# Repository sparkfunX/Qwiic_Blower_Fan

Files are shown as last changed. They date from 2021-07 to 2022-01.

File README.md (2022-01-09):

Qwiic Blower Fan
========================================

[Qwiic Blower Fan

[*Qwiic Blower Fan (SPX-18561)*](https://www.sparkfun.com/products/18561)

The unmistakable sounds of a tiny cooling fan spooling up usually means you've sat your laptop on a soft surface, or launched one too many tabs in your browser. It's a textbook cry for help from all of our favorite consumer electronics but what if your next hardware project could also complain about overheating? Well now it can!

In all seriousness, though, sometimes you need to move a little air around. Whether for active cooling or ventilation, a tiny fan can make a big difference. However, a tiny fan also has tiny wires which can make it difficult to work with. We've remedied this issue by mounting it to a board along with the mating flat-flex connector, a voltage booster and an ATtiny-based driver so you can power and control the fan over the Qwiic bus.

The control firmware monitors the tachometer output of the fan in order to implement PI Control over the fan speed, allowing you to set your desired speed in real units. It's also possible to disable the PI control loop and set the speed as a proportion of the maximum. The accompanying Arduino library includes example code for controlling the fan, tweaking settings, and even setting the fan speed based on an attached Qwiic Temperature Sensor and a lookup table.

We're unable to find a datasheet for this fan in particular (which is intended to replace the OEM fan in a Nintendo Switch)

Heads Up! This device draws enough power that it operates at the upper limit of the Qwiic bus. If there are few other devices on the bus and the fan is not allowed to rapidly change throttle, it is possible to power this fan directly from the bus. In some applications, however, it may be necessary to provide the blower fan with a dedicated 3.3V supply.

Repository Contents
-------------------

* **/Firmware** - Control firmware for the ATtiny
* **/Hardware** - Eagle design files (.brd, .sch)
* **/Production** - Panelized hardware files for production

License Information
-------------------

This product is _**open source**_! 

Please review the LICENSE.md file for license information. 

If you have any questions or concerns on licensing, please contact technical support on our [SparkFun forums](https://forum.sparkfun.com/viewforum.php?f=152).

Distributed as-is; no warranty is given.

- Your friends at SparkFun.

_<COLLABORATION CREDIT>_

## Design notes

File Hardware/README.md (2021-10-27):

# Qwiic_Blower_Fan
2-Wire Controllable Nintendo Switch Cooling Fan Breakout

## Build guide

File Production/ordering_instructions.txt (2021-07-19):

panel size, 147x152mm
PCB thickness, 1.6mm
number of layers, 2
soldermask color, Black
silkscreen color, White
oz copper, 1oz
finish, HASL lead free
stencils, top
pcs per panel, 6
min trace width, 0.1524mm / 0.0060in
min drill size, 0.3000mm / 0.0118in

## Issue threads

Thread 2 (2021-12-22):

Qwiic Fan Controller Firmware Bugs

dlkeng, 2021-12-22:
In reviewing and testing the "**Qwiic_Fan_Controller.ino**" firmware, I have observed and run into the following bugs:

1. In function `updateSettings()`: line **266**: What if `registerMap[WIRE_ADDR]` is an invalid I2C address? The `receiveEvent()` allows any value to be written to any register!
2. In function `requestEvent()`: line **388**: `requestEvent()` always writes 17 bytes. What if `registerIndex` is greater than zero? It will then return bytes beyond the end of `registerMap[]`! (not fatal, but not good!)
3. In function `receiveEvent()`: line **435**:
   -  What if `receivedCommands[0]` is an invalid register address? It will then allow bytes to be written beyond the end of `registerMap[]`!
   - What if `bytesReceived` is greater than `MAX_SENT_BYTES`? It will then allow whatever is in the memory beyond the end of `receivedCommands[]` to be written to `registerMap[]`!
   - What prevents writing beyond the end of `registerMap[]`? For example, assume `receivedCommands[0]` is `TRIMMER_DISABLE` and multiple bytes were sent. Any received bytes after the first one would be written to memory beyond the end of `registerMap[]`!

In summary, the `receiveEvent()` callback function has some serious memory integrity issues!

NPoole, 2021-12-30:
Thanks for the code review. Yeah this all looks about right.

1. I removed address validation during debugging and forgot to put it back
2. This is designed to wrap around so that you can read sequentially from every register but I forgot to implement the actual looping part. The fact that it always writes the entire register map is a consequence of the way the wire library ISRs work. It should be OK once it loops instead of wandering off into unknown memory.
3.  Same problem as 2 in reverse. I'll implement cyclic writes and register validation.

I'll correct these issues and make the new firmware available as soon as I can.

NPoole, 2022-01-09:
v11 addresses all of these issues to my satisfaction. Please feel free to check it out,

- Any address may be written to registerMap[WIRE_ADDR] but the address is validated before applying the change and committing it to EEPROM. If the address is outside of the valid range (0x08 to 0x77 inclusive)
- requestEvent() now writes all register values starting from the requested register to the end of the map and stops
- receiveEvent() can no longer write past the end of the register map, it will wrap around when it reaches the end

Please also keep in mind that the **current firmware now compiles to 8094 bytes and the target uC only has 8192 bytes of progmem**. While some features/fixes may not be robust, trade-offs have to be made. I believe (with the addition of i2c address validation) that any wayward register writes could now, in the worst case, be corrected by power cycling the device, which may not be a high bar to clear, but thanks to your testing we now clear it.

Closed 2022-01-09.

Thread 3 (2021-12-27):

QWIIC BLOWER FAN EXAMPLE FAILS TO RUN

JimKruk, 2021-12-27:
https://www.sparkfun.com/products/18561 Qwiic Blower Fan

downloaded the code from here: https://github.com/sparkfun/SparkFun_Qwiic_Fan_Arduino_Library

Example1_SetFanSpeed using a blackboard. when I plug in the USB the fan comes on before any code is downloaded. After compiling and downloading it see this error in setup:

Qwiic Blower Fan Example 1: Setting the Fan Speed
Device failed to setup - stopping
thoughts ?

dlkeng, 2021-12-29:
That is usually caused by the incorrect I2C address being used. By default, the **Qwiic Fan Arduino Library** uses the default I2C address of **0x36**. Your Sparkfun Qwicc Blower Fan has probably had its I2C address changed. You probably need to run an I2C scan sketch to determine what the I2C address your Sparkfun Qwicc Blower Fan is using.

Once you determine its I2C address, you can change the "_blower.begin()_" line in the Example1_SetFanSpeed to "_blower.begin(Wire,_ <your_I2C_address>_)_" and it should then work.

JimKruk, 2021-12-29:
Hi Dan
Here is the code I am using based on example1 I added a I2C scan function
but it says no devices found, When I try and pass a value of 36 I get a
compiler error,  I am using a blackboard and arduino 1.8.10

no matching function for call to 'PCFan::begin(int)'
thanks

/*
  This is a example written for the SparkFun Qwiic Blower Fan
  SparkFun sells these at its website: www.sparkfun.com
  Do you like this library? Help support SparkFun. Buy a board!
  https://www.sparkfun.com/products/18561

  Written by Nick Poole @ SparkFun Electronics, October 258h, 2021

  This example code demonstrates how to set and get the fan speed
  by randomly generating fan speeds between 0 and 8000 RPM
  and sending them to the board. It then reads the fan tachometer for
  comparison.

  https://github.com/sparkfun/SparkFun_Qwiic_Fan_Arduino_Library

  Development environment specifics:
  Arduino IDE 1.8.7

  This program is distributed in the hope that it will be useful,
  but WITHOUT ANY WARRANTY; without even the implied warranty of
  MERCHANTABILITY or FITNESS FOR A PARTICULAR PURPOSE. See the
  GNU General Public License for more details.

  You should have received a copy of the GNU General Public License
  along with this program.  If not, see <http://www.gnu.org/licenses/>.
*/

#include <SparkFun_Qwiic_Fan_Arduino_Library.h>
#include <Wire.h>
// Initialize the board
PCFan Blower;

void setup()
{
  Wire.begin();
  Serial.begin(115200);    // Start serial communication at 115200 baud
  scanI2C();
  Serial.println("Qwiic Blower Fan Example 1: Setting the Fan Speed");
  if (Blower.begin(36) == true) // Function to check if the board will ACK
  {
    Serial.println("Begin");
  }
  else
  {
    Serial.println("Device failed to setup - stopping");
    while (1); // Just sit and do nothing
  }
  Blower.disableFan();
}

void loop() {

  // Pick a random speed between 0 and 8000 RPM (In 1000 RPM increments)
  int randSpeed = random(0,8) * 1000;

  // Print the number to the terminal
  Serial.print("Setting Fan Speed to ");
  Serial.print(randSpeed);
  Serial.println(" RPM");

  // Set the fan speed
  Blower.setFanSpeed(randSpeed);

  // For the next 3 seconds, once per second, ask the board for a
tachometer reading
  // and report it to the terminal
  for(byte i = 0; i < 3; i++){
    delay(1000);
    Serial.print("Tachometer Reads ");
    Serial.print(Blower.getFanSpeed());
    Serial.println(" RPM");
  }

  // Print an empty line to make the terminal more readable
  Serial.println();
  delay(1000);

}

void scanI2C()
{
  byte error, address;
  int nDevices;

  Serial.println("Scanning I2C devices...");

 nDevices = 0;
 for (address = 1; address < 127; address++ )
  {
    // The i2c_scanner uses the return value of
    // the Write.endTransmisstion to see if
    // a device did acknowledge to the address.
    Wire.beginTransmission(address);
    error = Wire.endTransmission();

    if (error == 0)
    {
      Serial.print(F("I2C device found at address 0x"));
      Serial.println(address, HEX);
      nDevices++;

    }
    else if (error == 4)
    {
      Serial.print("Unknown error at address 0x");
      if (address < 16)
        Serial.print("0");
      Serial.println(address, HEX);
    }
  }

  // clear row 3 that was display i2c devices found

  if (nDevices == 0)
  {
    Serial.println("No I2C devices found\n");

  }
  else
  {
    Serial.print(nDevices);Serial.println(" I2C devices found");

  }
  delay(1000);           // wait 5 seconds for next scan

}

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

JimKruk, 2021-12-29:
fyi I added a second I2C device (TMP117) and it discovered that but not the
fan so the scan routine seems ok

Scanning I2C devices...
I2C device found at address 0x48
1 I2C devices found

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

PaulZC, 2021-12-29:
Hi @JimKruk ,

Which processor board are you using? If you're using an Artemis-based board, this might be a clock-stretching issue.

Have you tried ignoring the result of ```Blower.begin()```? What happens if you comment the ```while(1);  // Just sit and do nothing```? Does the rest of the code run normally?

Best wishes,
Paul

dlkeng, 2021-12-29:
Jim,
The fact you can scan and find another I2C device says you might have a problem with your Qwiic Blower Fan. Are you sure you are providing about 3.3V to it? You can measure it on the labeled point near the edge on the top or bottom of the board. Also, make sure your SDA and SCL (and GND) connections are all OK in the Qwiic wiring cable if that's what you're using.

If your Qwiic Blower Fan is getting power and your connections are OK, then you might have a defective Qwiic Blower Fan. If that's the case, I'm afraid I can't help you. (If you are familiar with electronics troubleshooting, you could also check that pin 2 of the 6-pin AVR ISP Connector holes on the back side of the board measures about 5V. If not, there could be a problem with the onboard U3 DC-DC Converter - see schematic. Everything on the Qwiic Blower Fan runs on 5V)

Also, two things about the use of the alternate "_button.begin()_". First, you are missing the "**Wire**" parameter and second, the address you used was decimal and you probably want the hex number with a leading '0x' (that's what the scan tool provides). That's why you had the compile error. The "_begin()_" optionally takes two parameters: **TwoWire &wirePort** and **uint8_t deviceAddress**.

JimKruk, 2021-12-29:
Hi Paul
I am using the sparkfun blackboard with a qwiic connection I am not home
right now but will try commenting out the loop and let you know. Kinda
doubt it will work since the i2c scanner does not see anything.
Thanks
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

JimKruk, 2021-12-29:
Hi Dan
Do you have an example of what I would code on the begin() line ? When I
get home home I will try and get some voltage measurements. I am using a
blackboard and a qwiic cable so no wiring per say.
Thanks

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

dlkeng, 2021-12-29:
Jim,
Assuming you can get the I2C scan to find your Fan, for example:
    `I2C device found at address 0x40`

then use:
  `if (Blower.begin(Wire, 0x40) == true)`

in place of the default: `if (Blower.begin() == true)`
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
JimKruk, 2022-01-05:
Awesome, thanks for the update Nick.  Btw Russell Turner from sf emailed me
about this also, not sure he is coordinating with you on this.

Curious, is this a firmware issue or just bad luck on the two fans I
received?
Thanks

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

NPoole, 2022-01-05:
I just messaged him to make sure we're not duplicating our efforts

It seems to me that there was no firmware on the unit that you received and right now we're trying to determine whether a few units were faulty or if an entire batch made it into stock without getting programmed.

JimKruk, 2022-01-05:
Ok, thanks.

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

JimKruk, 2022-01-06:
Hi Nick
I received replacement fans today, order # 6900103, still not working, the i2c scan routine does not detect it.  If it is a firmware update and something that is documented or someone has time to walk me through I am willing to try it vs mailing back and forth, let me know, thanks

JimKruk, 2022-01-07:
Hi Nick
Russell just replied and said you would take the lead on this. If you want me to attempt updating firmware and can walk me through it I’ll try.  I have no special hardware, etc but willing to try

JimKruk, 2022-01-10:
Hi Nick
Was wondering if you were able to get an updated firmware to work ?  I have four boards now if you want me to try and test something, thanks

NPoole, 2022-01-12:
Hi Jim!
Sorry for the delay. The problem you have isn't that you got a firmware that doesn't work, but that you didn't get any firmware at all. As far as I can tell, we've somehow sent you a number of completely unprogrammed units.

You could program the firmware on these units using a SparkFun Redboard/Arduino Uno/etc. as a programmer, if you want to attempt it, I'll give you instructions here. I've just tried it on my end to make sure it works.

**Step 1) Program Redboard with the ArduinoISP sketch**
Since you mentioned that you don't have a programmer on-hand, we're gonna use a Redboard (or other Uno-style Arduino board) as a programmer. The Arduino IDE actually includes the sketch for doing this as a Built-In Example.

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

Open this sketch and Upload it

**Step 2) Attach the RedBoard to your Qwiic Fan Blower**
Now you'll need to connect the RedBoard to the programming header on the Qwiic Blower Fan. The programming header is the 2x3 pin header on the backside of the board. I soldered pins to mine during firmware development, and this is the most reliable way, but you could theoretically just push header pins against it to make a temporary connection.

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

Here is the pinout of the Qwiic Blower programming header. Pin 1 is the one marked with a line on the silkscreen:
```
Pin 1*: MISO  | Pin 2: 3.3V
Pin 3: SCK    | Pin 4: MOSI
Pin 5: D10    | Pin 6: GND
```

**Step 3) Install the board package**
Before you can program the Qwiic Blower, you'll need the Arduino Board Package for the attiny841 that the board is based on. You can do this through the Arduino Board Manager. Search "attinycore" and install the package as shown

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

**Step 4) Open the firmware in Arduino**
You can find the firmware Arduino sketch in this repo. Either clone the repo or download the zip file and open "Qwiic_Fan_Controller" in the \Firmware directory.

**Step 5) Set the board options**
There are a number of options that need to be correctly selected in order for the firmware to be compiled for the correct target. Here is a screenshot of the correct options. Make sure your menu matches this (the COM port doesn't matter)

**Step 6) Select "Arduino as ISP" as your programmer**

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

**Step 7) Run the "Burn Bootloader" option in the "Tools" menu**
Even though we've selected the No Bootloader version of the board profile, we still need to run "Burn Bootloader" in order to setup the attiny chip according to the selections we made in the tools menu. It should take a few moments. If it's successful, you should see "avrdude done.  Thank you." in the output pane. If it fails, check your wiring.

**Step 8) Program the firmware**
You should now be able to select the "Upload" or "Upload using Programmer" option and program the firmware to the board. This will take a few minutes because of the throughput limitations of the "Arduino as ISP" setup. Your output pane will look like this while it's writing:

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

Once this is finished, the board should be programmed. If you decide to attempt this, please let me know how it goes.
I'm going to close this issue for now. If you wouldn't mind carrying on the conversation with me at **Nick.Poole@SparkFun.com** we'll continue to troubleshoot and hopefully get you some working units soon!

Closed 2022-01-12.

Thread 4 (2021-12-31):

Qwiic Fan Controller Firmware Possible Divide-by-Zero Errors

dlkeng, 2021-12-31:
In testing the "**Qwiic_Fan_Controller.ino**" firmware, I have observed and run into the following possible divide-by-zero errors:

In function `readTachometer()`:
 - Line 329: If variable `tach` is zero (not likely, but possible)
 - Line 330: If `registerMap[FAN_TACH_DIVIDER]` is zero (possible since is controlled over I2C bus)

In my simulated testing on an Arduino Nano with Arduino 1.8.13, it appears that either of the above cases can crash the firmware or cause other incorrect operations, including infinitely clock-stretching SCL on the I2C bus in response to an I2C bus transaction.

NPoole, 2022-01-09:
Thanks for sniffing this out, v11 fixes this

Closed 2022-01-09.

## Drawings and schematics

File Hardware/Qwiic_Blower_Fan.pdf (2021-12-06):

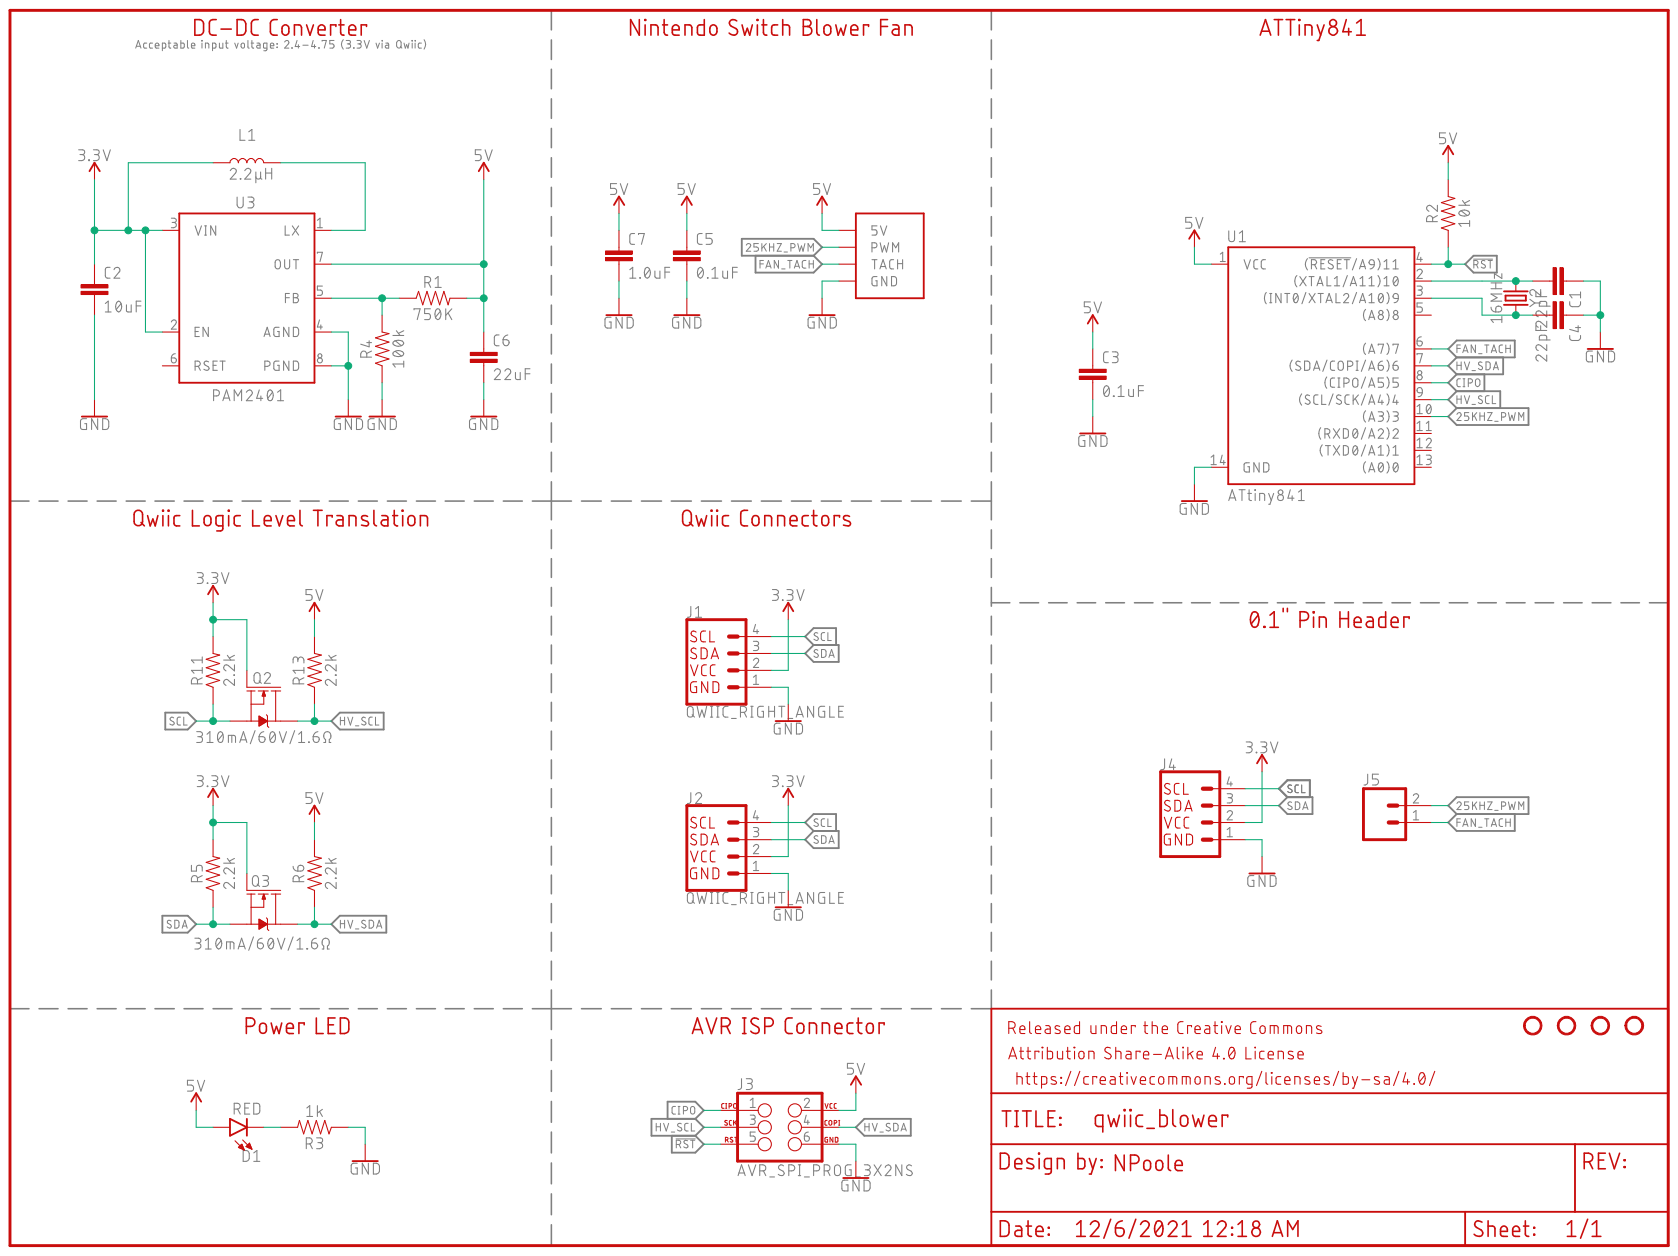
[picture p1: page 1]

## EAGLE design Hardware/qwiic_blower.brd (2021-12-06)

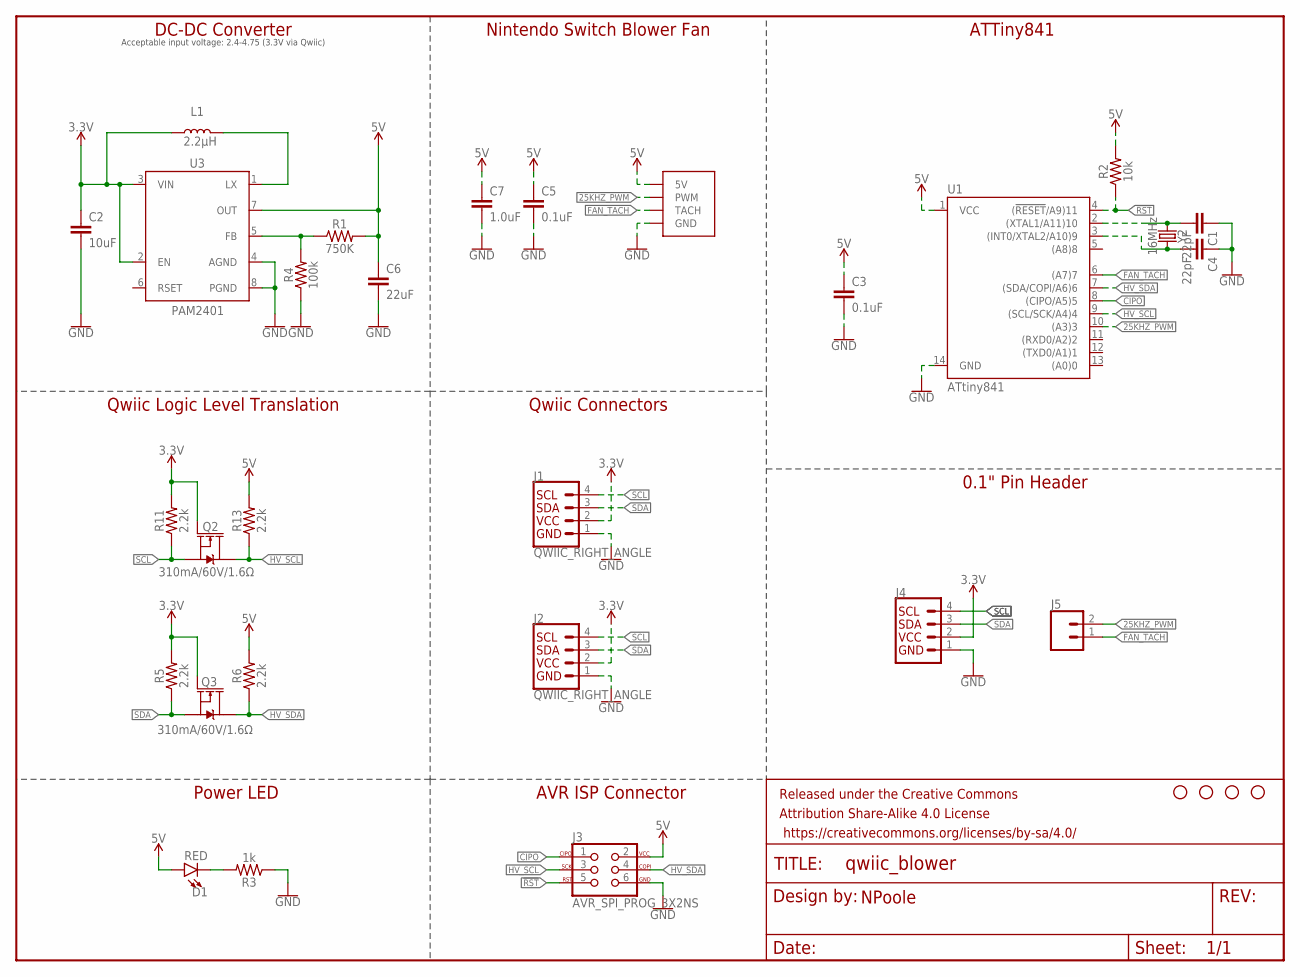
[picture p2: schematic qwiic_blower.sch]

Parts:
C1, C4: 22pF; 0603
C2: 10uF; 0603
C3, C5: 0.1uF; 0603
C6: 22uF; 0805
C7: 1.0uF; 0603
D1: RED; LED-0603
FRAME1: FRAME-LETTER; CREATIVE_COMMONS
H1, H2, H3, H4: STAND-OFF
J1, J2: QWIIC_RIGHT_ANGLE; JST04_1MM_RA
J3: AVR_SPI_PROG_3X2NS; 2X3-NS
J4: I2C_STANDARD_NO_SILK; 1X04_NO_SILK
J5: CONN_021X02_NO_SILK; 1X02_NO_SILK
L1: 2.2μH; 0806
Q2, Q3: 310mA/60V/1.6Ω; SOT323
R1: 750K; 0603
R2: 10k; 0603
R3: 1k; 0603
R4: 100k; 0603
R5, R6, R11, R13: 2.2k; 0603
U1: ATtiny841; SO14
U3: PAM2401; MSOP8
U$19: NINTENDO_SWITCH_FAN; FPC_4_0.5MM
Y2: 16MHz; CRYSTAL-SMD-2.0X1.6MM

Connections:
3.3V: C2.1, J1.2, J2.2, J4.2, L1.1, Q2.1 (G), Q3.1 (G), R5.2, R11.2, U3.2 (EN), U3.3 (VIN)
5V: C3.1, C5.1, C6.1, C7.1, D1.A, J3.2, R1.2, R2.2, R6.2, R13.2, U1.1 (VCC), U3.7 (OUT), U$19.1 (5V)
25KHZ_PWM: J5.2, U1.10 ((A3)3), U$19.4 (PWM)
!RST: J3.5, R2.1, U1.4 ((!RESET!/A9)11)
CIPO: J3.1, U1.8 ((CIPO/A5)5)
FAN_TACH: J5.1, U1.6 ((A7)7), U$19.2 (TACH)
GND: C1.1, C2.2, C3.2, C4.1, C5.2, C6.2, C7.2, J1.1, J2.1, J3.6, J4.1, R3.1, R4.1, U1.14 (GND), U3.4 (AGND), U3.8 (PGND), U$19.3 (GND)
HV_SCL: J3.3, Q2.3 (D), R13.1, U1.9 ((SCL/SCK/A4)4)
HV_SDA: J3.4, Q3.3 (D), R6.1, U1.7 ((SDA/COPI/A6)6)
unnamed: C4.2, U1.3 ((INT0/XTAL2/A10)9), Y2.1
unnamed: R1.1, R4.2, U3.5 (FB)
unnamed: L1.2, U3.1 (LX)
unnamed: C1.2, U1.2 ((XTAL1/A11)10), Y2.3 (2)
unnamed: D1.C, R3.2
SCL: J1.4, J2.4, J4.4, Q2.2 (S), R11.1
SDA: J1.3, J2.3, J4.3, Q3.2 (S), R5.1

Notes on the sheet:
DC-DC Converter
Acceptable input voltage: 2.4-4.75 (3.3V via Qwiic)
Nintendo Switch Blower Fan
ATTiny841
Qwiic Connectors
Qwiic Logic Level Translation
0.1" Pin Header
AVR ISP Connector
Power LED
NPoole

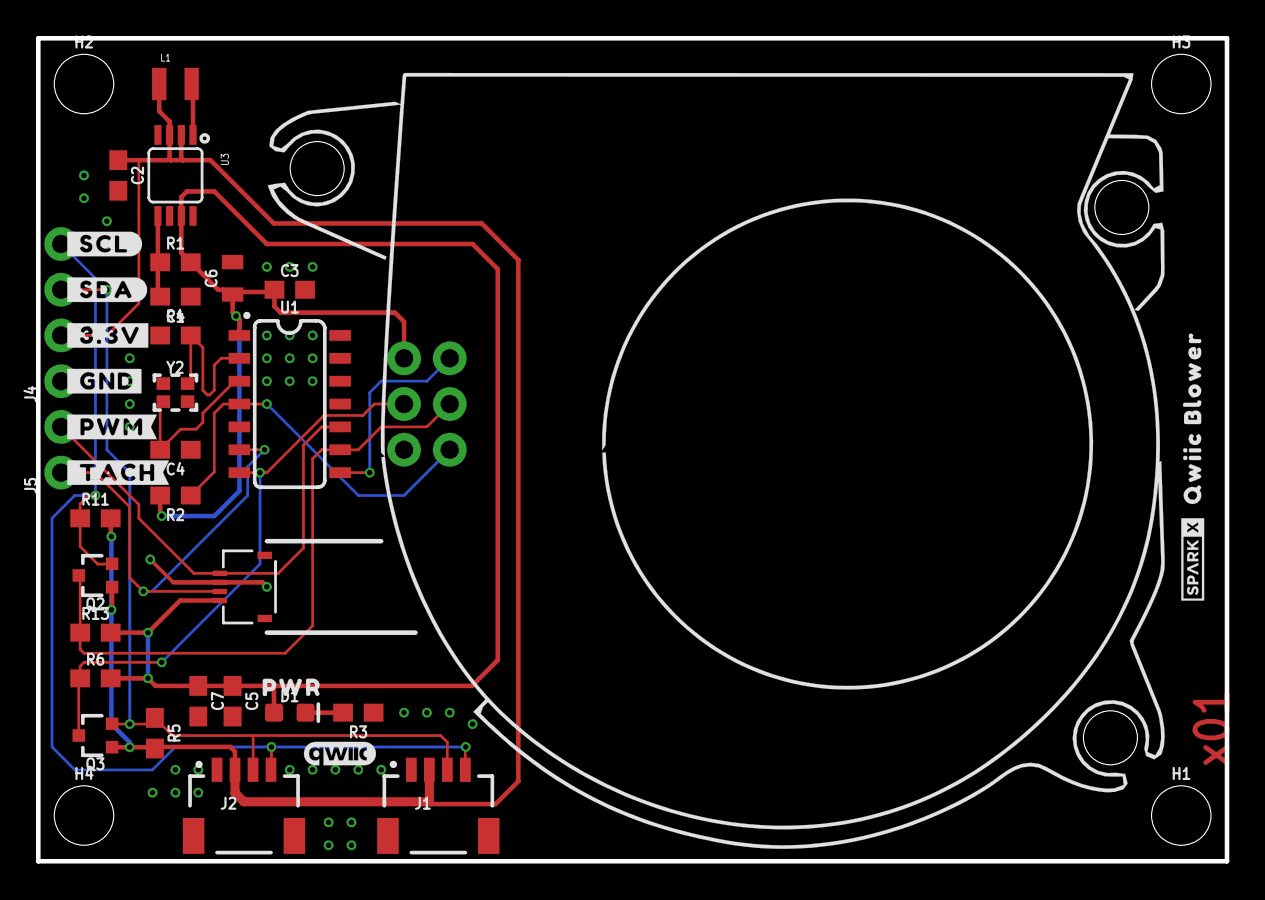
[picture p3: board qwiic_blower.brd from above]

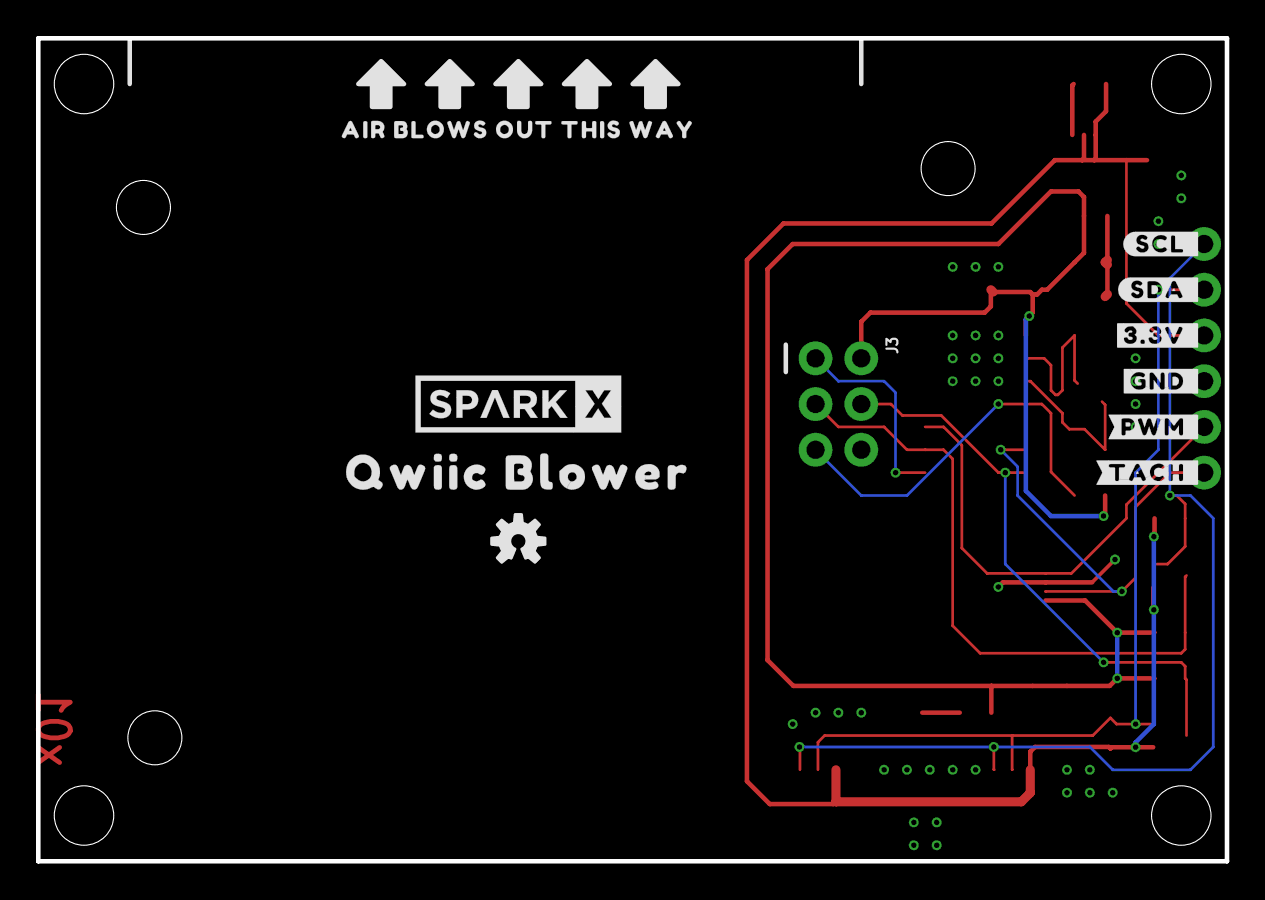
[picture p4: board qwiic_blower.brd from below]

Board: 2 copper layers, 66.0 x 45.7 mm, 53 parts (11 on the bottom side), 16 nets.

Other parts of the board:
U$1: #_TACH#0
U$2: #_PWM#0
U$3: #_GND#0
U$4: #_3#3V#0
U$5: #_SDA#0
U$6: #_SCL#0
U$7: #SCL_#0
U$8: #SDA_#0
U$9: #3#3V_#0
U$10: #GND_#0
U$11: #PWM_#0
U$12: #TACH_#0
U$13: QWIIC_4MM
U$14: QWIIC_BLOWER0
U$15: SPARKX-TINY
U$16: AIR_BLOWS_OUT_THIS_WAY0
U$17: _QWIIC_BLOWER_0
U$18: SPARKX-LARGE
U$20: OSHW-LOGO-S
U$21: PWR0

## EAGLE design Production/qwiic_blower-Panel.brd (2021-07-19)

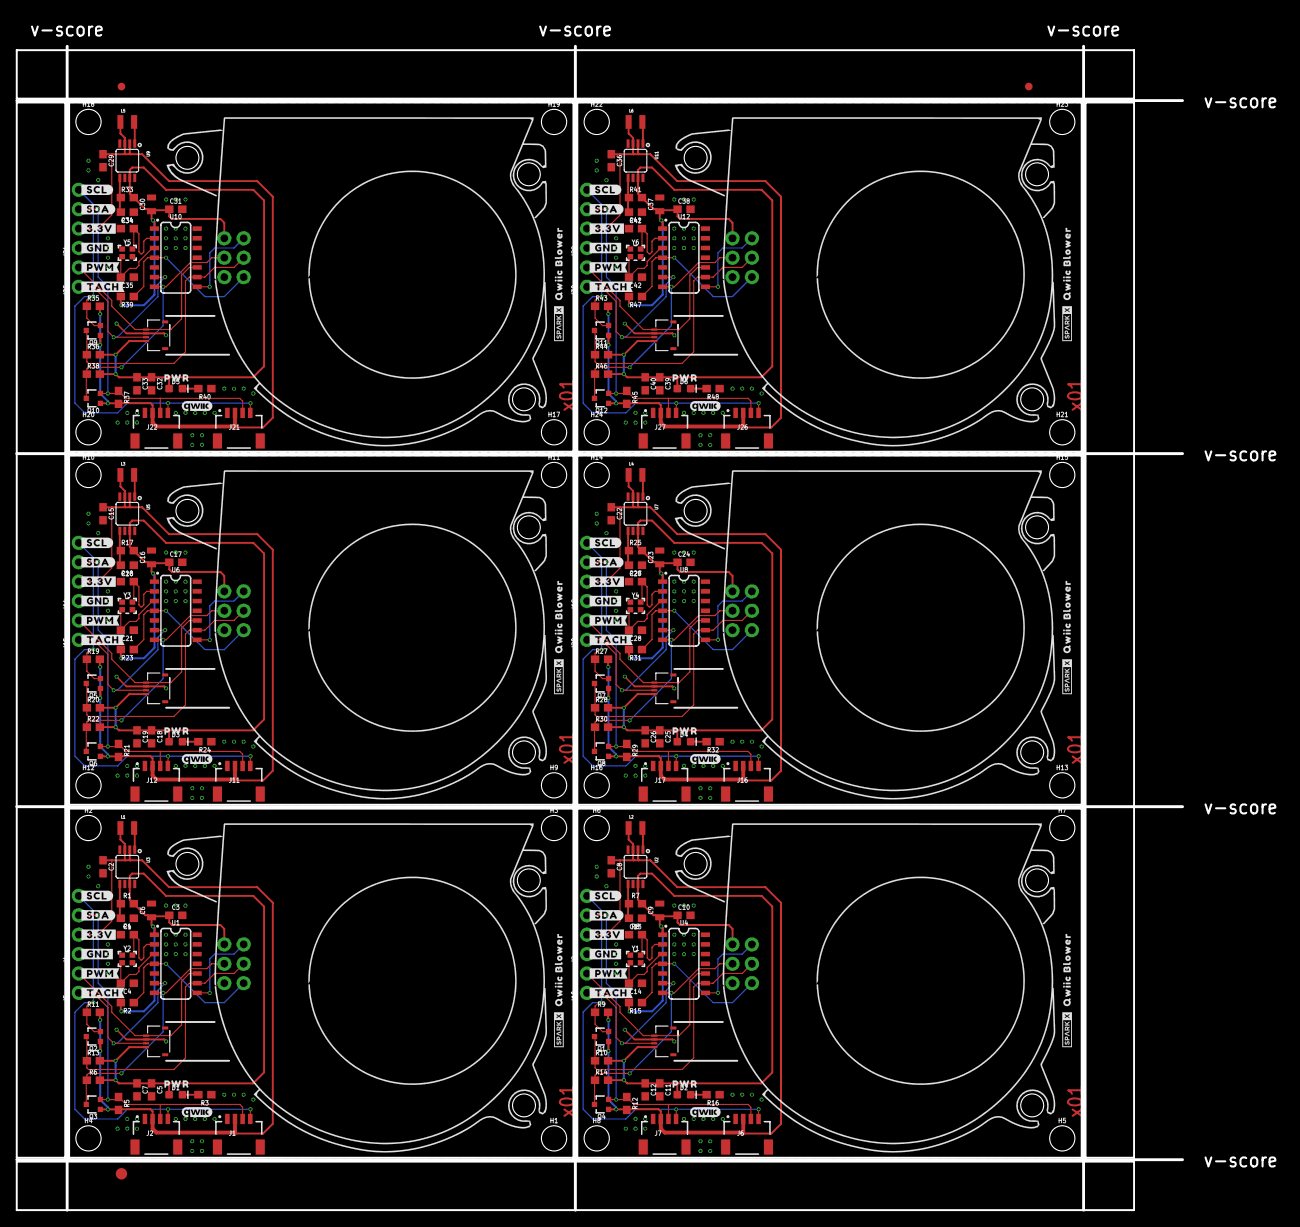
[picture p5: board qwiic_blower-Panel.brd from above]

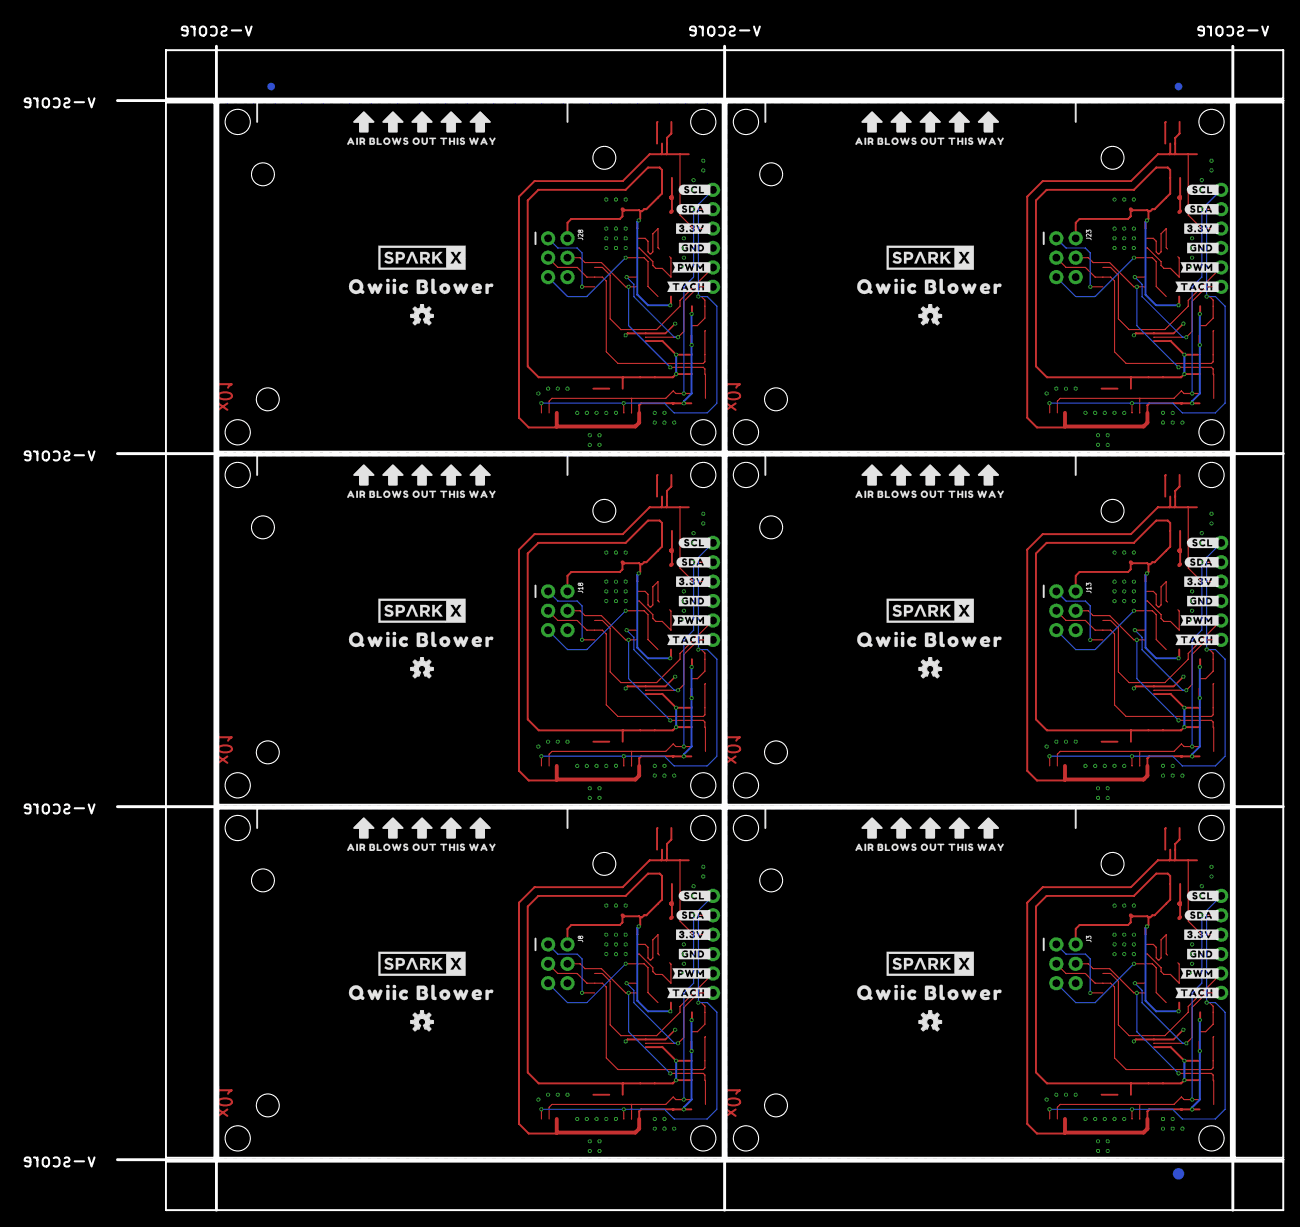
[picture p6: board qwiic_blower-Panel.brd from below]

Board: 2 copper layers, 152.7 x 152.4 mm, 318 parts (69 on the bottom side), 96 nets.

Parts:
C1, C4, C13, C14, C20, C21, C27, C28, C34, C35, C41, C42: 22pF; 0603
C2, C8, C15, C22, C29, C36: 10uF; 0603
C3, C5, C10, C11, C17, C18, C24, C25, C31, C32, C38, C39: 0.1uF; 0603
C6, C9, C16, C23, C30, C37: 22uF; 0805
C7, C12, C19, C26, C33, C40: 1.0uF; 0603
D1, D2, D3, D4, D5, D6: RED; LED-0603
E$1, E$2, E$3, E$4: FIDUCIAL-1X2
E$5, E$6: FIDUCIAL-1.5X3
H1, H2, H3, H4, H5, H6, H7, H8, H9, H10, H11, H12, H13, H14, H15, H16, H17, H18, H19, H20, H21, H22, H23, H24: STAND-OFF
J1, J2, J6, J7, J11, J12, J16, J17, J21, J22, J26, J27: QWIIC_RIGHT_ANGLE; JST04_1MM_RA
J3, J8, J13, J18, J23, J28: AVR_SPI_PROG_3X2NS; 2X3-NS
J4, J9, J14, J19, J24, J29: 1X04_NO_SILK
J5, J10, J15, J20, J25, J30: 1X02_NO_SILK
L1, L2, L3, L4, L5, L6: 2.2μH; 0806
Q1, Q2, Q3, Q4, Q5, Q6, Q7, Q8, Q9, Q10, Q11, Q12: 310mA/60V/1.6Ω; SOT323
R1, R7, R17, R25, R33, R41: 750K; 0603
R2, R15, R23, R31, R39, R47: 10k; 0603
R3, R16, R24, R32, R40, R48: 1k; 0603
R4, R8, R18, R26, R34, R42: 100k; 0603
R5, R6, R9, R10, R11, R12, R13, R14, R19, R20, R21, R22, R27, R28, R29, R30, R35, R36, R37, R38, R43, R44, R45, R46: 2.2k; 0603
U1, U4, U6, U8, U10, U12: ATtiny841; SO14
U2, U3, U5, U7, U9, U11: PAM2401; MSOP8
U$1, U$22, U$43, U$64, U$85, U$106: #_TACH#0
U$2, U$23, U$44, U$65, U$86, U$107: #_PWM#0
U$3, U$24, U$45, U$66, U$87, U$108: #_GND#0
U$4, U$25, U$46, U$67, U$88, U$109: #_3#3V#0
U$5, U$26, U$47, U$68, U$89, U$110: #_SDA#0
U$6, U$27, U$48, U$69, U$90, U$111: #_SCL#0
U$7, U$28, U$49, U$70, U$91, U$112: #SCL_#0
U$8, U$29, U$50, U$71, U$92, U$113: #SDA_#0
U$9, U$30, U$51, U$72, U$93, U$114: #3#3V_#0
U$10, U$31, U$52, U$73, U$94, U$115: #GND_#0
U$11, U$32, U$53, U$74, U$95, U$116: #PWM_#0
U$12, U$33, U$54, U$75, U$96, U$117: #TACH_#0
U$13, U$34, U$55, U$76, U$97, U$118: QWIIC_4MM
U$14, U$35, U$56, U$77, U$98, U$119: QWIIC_BLOWER0
U$15, U$36, U$57, U$78, U$99, U$120: SPARKX-TINY
U$16, U$37, U$58, U$79, U$100, U$121: AIR_BLOWS_OUT_THIS_WAY0
U$17, U$38, U$59, U$80, U$101, U$122: _QWIIC_BLOWER_0
U$18, U$39, U$60, U$81, U$102, U$123: SPARKX-LARGE
U$19, U$40, U$61, U$82, U$103, U$124: NINTENDO_SWITCH_FAN; FPC_4_0.5MM
U$20, U$41, U$62, U$83, U$104, U$125: OSHW-LOGO-S
U$21, U$42, U$63, U$84, U$105, U$126: PWR0
Y1, Y2, Y3, Y4, Y5, Y6: 16MHz; CRYSTAL-SMD-2.0X1.6MM

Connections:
3.3V: C2.1, J1.2, J2.2, J4.2, L1.1, Q2.1, Q3.1, R5.2, R11.2, U3.2, U3.3
3.3V1: C8.1, J6.2, J7.2, J9.2, L2.1, Q1.1, Q4.1, R9.2, R12.2, U2.2, U2.3
3.3V2: C15.1, J11.2, J12.2, J14.2, L3.1, Q5.1, Q6.1, R19.2, R21.2, U5.2, U5.3
3.3V3: C22.1, J16.2, J17.2, J19.2, L4.1, Q7.1, Q8.1, R27.2, R29.2, U7.2, U7.3
3.3V4: C29.1, J21.2, J22.2, J24.2, L5.1, Q9.1, Q10.1, R35.2, R37.2, U9.2, U9.3
3.3V5: C36.1, J26.2, J27.2, J29.2, L6.1, Q11.1, Q12.1, R43.2, R45.2, U11.2, U11.3
5V: C3.1, C5.1, C6.1, C7.1, D1.A, J3.2, R1.2, R2.2, R6.2, R13.2, U1.1, U3.7, U$19.1
5V1: C9.1, C10.1, C11.1, C12.1, D2.A, J8.2, R7.2, R10.2, R14.2, R15.2, U2.7, U4.1, U$40.1
5V2: C16.1, C17.1, C18.1, C19.1, D3.A, J13.2, R17.2, R20.2, R22.2, R23.2, U5.7, U6.1, U$61.1
5V3: C23.1, C24.1, C25.1, C26.1, D4.A, J18.2, R25.2, R28.2, R30.2, R31.2, U7.7, U8.1, U$82.1
5V4: C30.1, C31.1, C32.1, C33.1, D5.A, J23.2, R33.2, R36.2, R38.2, R39.2, U9.7, U10.1, U$103.1
5V5: C37.1, C38.1, C39.1, C40.1, D6.A, J28.2, R41.2, R44.2, R46.2, R47.2, U11.7, U12.1, U$124.1
25KHZ_PWM: J5.2, U1.10, U$19.4
25KHZ_PWM1: J10.2, U4.10, U$40.4
25KHZ_PWM2: J15.2, U6.10, U$61.4
25KHZ_PWM3: J20.2, U8.10, U$82.4
25KHZ_PWM4: J25.2, U10.10, U$103.4
25KHZ_PWM5: J30.2, U12.10, U$124.4
!RST: J3.5, R2.1, U1.4
!RST1: J8.5, R15.1, U4.4
!RST2: J13.5, R23.1, U6.4
!RST3: J18.5, R31.1, U8.4
!RST4: J23.5, R39.1, U10.4
!RST5: J28.5, R47.1, U12.4
CIPO: J3.1, U1.8
CIPO1: J8.1, U4.8
CIPO2: J13.1, U6.8
CIPO3: J18.1, U8.8
CIPO4: J23.1, U10.8
CIPO5: J28.1, U12.8
FAN_TACH: J5.1, U1.6, U$19.2
FAN_TACH1: J10.1, U4.6, U$40.2
FAN_TACH2: J15.1, U6.6, U$61.2
FAN_TACH3: J20.1, U8.6, U$82.2
FAN_TACH4: J25.1, U10.6, U$103.2
FAN_TACH5: J30.1, U12.6, U$124.2
GND: C1.1, C2.2, C3.2, C4.1, C5.2, C6.2, C7.2, J1.1, J2.1, J3.6, J4.1, R3.1, R4.1, U1.14, U3.4, U3.8, U$19.3
GND1: C8.2, C9.2, C10.2, C11.2, C12.2, C13.1, C14.1, J6.1, J7.1, J8.6, J9.1, R8.1, R16.1, U2.4, U2.8, U4.14, U$40.3
GND2: C15.2, C16.2, C17.2, C18.2, C19.2, C20.1, C21.1, J11.1, J12.1, J13.6, J14.1, R18.1, R24.1, U5.4, U5.8, U6.14, U$61.3
GND3: C22.2, C23.2, C24.2, C25.2, C26.2, C27.1, C28.1, J16.1, J17.1, J18.6, J19.1, R26.1, R32.1, U7.4, U7.8, U8.14, U$82.3
GND4: C29.2, C30.2, C31.2, C32.2, C33.2, C34.1, C35.1, J21.1, J22.1, J23.6, J24.1, R34.1, R40.1, U9.4, U9.8, U10.14, U$103.3
GND5: C36.2, C37.2, C38.2, C39.2, C40.2, C41.1, C42.1, J26.1, J27.1, J28.6, J29.1, R42.1, R48.1, U11.4, U11.8, U12.14, U$124.3
HV_SCL: J3.3, Q2.3, R13.1, U1.9
HV_SCL1: J8.3, Q1.3, R10.1, U4.9
HV_SCL2: J13.3, Q5.3, R20.1, U6.9
HV_SCL3: J18.3, Q7.3, R28.1, U8.9
HV_SCL4: J23.3, Q9.3, R36.1, U10.9
HV_SCL5: J28.3, Q11.3, R44.1, U12.9
HV_SDA: J3.4, Q3.3, R6.1, U1.7
HV_SDA1: J8.4, Q4.3, R14.1, U4.7
HV_SDA2: J13.4, Q6.3, R22.1, U6.7
HV_SDA3: J18.4, Q8.3, R30.1, U8.7
HV_SDA4: J23.4, Q10.3, R38.1, U10.7
HV_SDA5: J28.4, Q12.3, R46.1, U12.7
unnamed: C4.2, U1.3, Y2.1
unnamed: R1.1, R4.2, U3.5
unnamed: L1.2, U3.1
unnamed: C1.2, U1.2, Y2.3
unnamed: D1.C, R3.2
unnamed: R7.1, R8.2, U2.5
unnamed: L2.2, U2.1
unnamed: C14.2, U4.3, Y1.1
unnamed: C13.2, U4.2, Y1.3
unnamed: D2.C, R16.2
unnamed: R17.1, R18.2, U5.5
unnamed: L3.2, U5.1
unnamed: C21.2, U6.3, Y3.1
unnamed: C20.2, U6.2, Y3.3
unnamed: D3.C, R24.2
unnamed: R25.1, R26.2, U7.5
unnamed: L4.2, U7.1
unnamed: C28.2, U8.3, Y4.1
unnamed: C27.2, U8.2, Y4.3
unnamed: D4.C, R32.2
unnamed: R33.1, R34.2, U9.5
unnamed: L5.2, U9.1
unnamed: C35.2, U10.3, Y5.1
unnamed: C34.2, U10.2, Y5.3
unnamed: D5.C, R40.2
unnamed: R41.1, R42.2, U11.5
unnamed: L6.2, U11.1
unnamed: C42.2, U12.3, Y6.1
unnamed: C41.2, U12.2, Y6.3
unnamed: D6.C, R48.2
SCL: J1.4, J2.4, J4.4, Q2.2, R11.1
SCL1: J6.4, J7.4, J9.4, Q1.2, R9.1
SCL2: J11.4, J12.4, J14.4, Q5.2, R19.1
SCL3: J16.4, J17.4, J19.4, Q7.2, R27.1
SCL4: J21.4, J22.4, J24.4, Q9.2, R35.1
SCL5: J26.4, J27.4, J29.4, Q11.2, R43.1
SDA: J1.3, J2.3, J4.3, Q3.2, R5.1
SDA1: J6.3, J7.3, J9.3, Q4.2, R12.1
SDA2: J11.3, J12.3, J14.3, Q6.2, R21.1
SDA3: J16.3, J17.3, J19.3, Q8.2, R29.1
SDA4: J21.3, J22.3, J24.3, Q10.2, R37.1
SDA5: J26.3, J27.3, J29.3, Q12.2, R45.1

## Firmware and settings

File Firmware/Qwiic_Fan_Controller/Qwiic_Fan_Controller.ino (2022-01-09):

#include <Wire.h>
#include <EEPROM.h>
#include <PIDController.h> // https://github.com/DonnyCraft1/PIDArduino

/****************************************************
 * HARDWARE CONFIGURATION
 * This firmware is used on multiple boards with minor
 * hardware differences so BE CAREFUL to define the 
 * correct hardware configuration below before 
 * programming!
****************************************************/
//#define QWIIC_PC_FAN_CONTROLLER // SPX-18570
#define QWIIC_BLOWER // SPX-18561

#ifdef QWIIC_PC_FAN_CONTROLLER
#define TRIM_DISABLE_DEFAULT 0x00
#endif
#ifdef QWIIC_BLOWER
#define TRIM_DISABLE_DEFAULT 0xFF
#endif 

/* PIN ASSIGNMENTS */
#define PIN_TRIM_KI 0    // ADC in from trimpot
#define PIN_TRIM_KP 1    // ADC in from trimpot
#define PIN_FAN_ENABLE 2 // DO to !FAN_EN
#define PIN_PWM_OUT 3    // DO to FAN_PWM
#define PIN_TACH_IN 7    // DI from FAN_TACH

/* I²C STUFF */
#define MAX_SENT_BYTES 0x05 // Used to ignore invalid commands
#define DEFAULT_ADDR 0x36   // Factory Default Peripheral Address

/* REGISTER MAP */
#define WIRE_ADDR 0x00             // Device Address
#define FAN_ENABLE 0x01            // Enable power to fan VCC pin (0xFF to enable)
#define SETPOINT_RPM 0x02          // PI Controller setpoint in RPM (2 bytes unsigned integer)
#define KP_VALUE 0x04              // PI Controller Proportional Term (2 bytes signed fixed decimal) \
                                   // Setting this parameter from the I²C Controller overrides the onboard trimpot
#define KI_VALUE 0x06              // PI Controller Integral Term (2 bytes signed fixed decimal) \
                                   // Setting this parameter from the I²C Controller overrides the onboard trimpot
#define FAN_TACH_DIVIDER 0x08      // Pulses per rotation indicated by fan/blower datasheet (usually 2)
#define FAN_ACTUAL_RPM 0x09        // Fan Speed Actual as indicated by Tachometer, input to PI Controller (2 bytes integer)
#define PI_OUT 0x0B                // Output of PI Controller for debugging (2 bytes integer)
#define PI_LOOP_DISABLE 0x0D       // Disable PI Controller and use contents of PROPORTIONAL_THROTTLE as speed (0xFF for Disable)
#define PROPORTIONAL_THROTTLE 0x0E // Fan speed as % of MAX. Inverse of PWM Width Cycle.                          \
                                   // When PI Controller is Enabled this register contains its output x (100/320) \
                                   // Whem PI Controller is Disabled the PWM Width Cycle is set to this register's inverse
#define TRIMMER_SCALE 0x0F         // Trimpot values are multiplied by this number. Probably only useful in edge cases. 2.0 (20) by default.
#define TRIMMER_DISABLE 0x10       // Stop reading trimpot ADCs and only use values written to the Kx_VALUE register by the I²C Controller (0xFF for Disable)
#define FW_VERSION 0x11            // Firmware version 

/* EEPROM MAP */
#define EEPROM_DEV_ADDR 0x00        // Because the I²C device address is user selectable, we need to remember it between boot cycles

/* MISCELLANEOUS GLOBAL VARS */
uint8_t receivedCommands[MAX_SENT_BYTES]; // I²C command buffer
uint8_t wire_addr = DEFAULT_ADDR;         // I²C device address
bool changeFlag = 0;                      // Use this flag to alert the main loop when a register change requires attention
uint8_t registerIndex = 0;                // Use this to track our position in the device registers during consecutive read operations

/****************************************************
 * SET THE REGISTER MAP DEFAULTS
 * These are the bus-accessible device registers
 * and their default values */
uint8_t registerMap[0x12] = 
    {
        0x00,                   // WIRE_ADDR
        0x00,                   // FAN_ENABLE
        0x00,                   // SETPOINT_RPM
        0x00,                   // SETPOINT_RPM BYTE 2
        0,                      // KP_VALUE (70 interpreted as 2.50)
        250,                     // KP_VALUE BYTE 2 
        1,                      // KP_VALUE (390 interpreted as 3.90)
        134,                     // KP_VALUE BYTE 2
        2,                   // FAN_TACH_DIVIDER (2 pulses per rotation)
        0x00,                   // FAN_ACTUAL_RPM 
        0x00,                   // FAN_ACTUAL_RPM BYTE 2
        0x00,                   // PI_OUT
        0x00,                   // PI_OUT BYTE 2
        0x00,                   // PI_LOOP_DISABLE (enabled)
        0x00,                   // PROPORTIONAL_THROTTLE
        20,                   // TRIMMER_SCALE (20 interpreted as 2.0)
        TRIM_DISABLE_DEFAULT,    // TRIMMER_DISABLE
        11                      // FIRMWARE VERSION 1.1
    };
/****************************************************/

// Instantiate PI Controller
PIDController piController;

void setup()
{
    // Check EEPROM for a bus address and set accordingly
    setWireAddress();

    // Setup timers for 25kHz Fast PWM
    fastPWMSetup();

    // Set the initial pin states
    pinMode(PIN_PWM_OUT, OUTPUT);
    pinMode(PIN_TACH_IN, INPUT_PULLUP); // Fan Tachometer is open-collector
    pinMode(PIN_FAN_ENABLE, OUTPUT);
    digitalWrite(PIN_FAN_ENABLE, HIGH); // Fan Enable is active low. Boot disabled to avoid hard start
    pinMode(PIN_TRIM_KI, INPUT);
    pinMode(PIN_TRIM_KP, INPUT);

    // Start I2C
    Wire.begin(wire_addr);
    Wire.onRequest(requestEvent);
    Wire.onReceive(receiveEvent);

    // Start the PI Controller
    piController.begin();
    piController.limit(20, 320); // Limit the PI output to prevent integral windup
}

void loop()
{
    // Get the tachometer reading, turn it into a real RPM using the value from
    // FAN_TACH_DIVIDER, and stuff it into FAN_ACTUAL_RPM for the I²C controller
    // to query and for the PI controller to compute against.
    readTachometer();

    // Finding which device register has been changed and updating
    // the approptiate settings takes some time so we only do it if
    // the registers have been poked. This way, we interfere as little
    // as possible with the PI Controller and PWM Generator
    if (changeFlag)
    {
        updateSettings();
    }

    // If the hardware is a Qwiic 4-Wire Fan Controller and the TRIMMER_DISABLE flag isn't set
    // then read the trimmers, apply the correct scale and offset, and then load those
    // values into the Kx_VALUE registers. If the TRIMMER_DISABLE flag is set, or this is
    // a Qwiic Blower board without trimpots, we skip reading the trimpots, so whatever
    // value is in the Kx_VALUE register from the last I²C receive is used for tuning.
    if (registerMap[TRIMMER_DISABLE] != 0xFF)
    {
        readTrimmers();
    }

    // Check whether the user has disabled the control loop in
    // favor of direct proportional speed control. If so, set
    // the PWM Width according to the contents of PROPORTIONAL_THROTTLE
    // if not, compute the output of the PI controller from the
    // contents of SETPOINT_RPM
    if (registerMap[PI_LOOP_DISABLE] == 0xFF)
    {
        pwmWidth(map(registerMap[PROPORTIONAL_THROTTLE], 0, 100, 0, 320));
    }
    else
    {
        piUpdate();
    }
}

/****************************************************
 * Function piUpdate()
 * The PID library has a 'compute' function, which we do
 * call in this method. However, in our particular case, 
 * it's easier to package that up with the tuning functions
 * becuase we always update our tunings before calculating 
 * the output. It seems excessive but it costs us less time
 * to just update the tunings than it does to check whether
 * it's necessary. We also use this method to update the
 * output value in the register map. 
****************************************************/
void piUpdate()
{

    float proportional = 0;
    float integral = 0;
    uint16_t setpoint = 0;
    uint16_t piOutput = 0;
    uint16_t tachReading = 0;

    // Expand the registerMap values back into int16
    // Multiply by 0.01 as neccessary to move the decimal into
    // the right position
    proportional += registerMap[KP_VALUE] << 8;
    proportional += registerMap[KP_VALUE + 0x01];
    proportional *= 0.01;

    integral += registerMap[KI_VALUE] << 8;
    integral += registerMap[KI_VALUE + 0x01];
    integral *= 0.01;

    setpoint += registerMap[SETPOINT_RPM] << 8;
    setpoint += registerMap[SETPOINT_RPM + 0x01];

    tachReading += registerMap[FAN_ACTUAL_RPM] << 8;
    tachReading += registerMap[FAN_ACTUAL_RPM + 0x01];

    // PC Fans tend to have a dead zone at the low end, so we limit the PI controller
    // to the range above this dead zone (to prevent stalling the fan and setting up
    // an oscillation) This does mean, however, that the PI controller will never 
    // organically output a 0, so if the fan speed is set to 0 we need to override the
    // PI controller
    if(setpoint !=0){

      // Update the PI Controller
      piController.setpoint(setpoint);
      piController.tune(proportional, integral, 0);
      piOutput = piController.compute(tachReading);

    }else{

      piOutput = 0;
      
    }

    // Update the PI_OUT register entry
    registerMap[PI_OUT] = piOutput >> 8;
    registerMap[PI_OUT + 0x01] = piOutput;

    // Actually set the fan PWM output
    pwmWidth(piOutput);
}

/****************************************************
 * Function readTrimmerAndTune()
 * Read the Trimpots, process them according to the 
 * scaling and offset registers, constrain them to 
 * the size of the Kx_VALUE registers, and store 
 * them for reference when tuning the PI Controller
****************************************************/
void readTrimmers()
{

    // Read ADCs into some temp vars
    // The data types are a little weird because of trying to make them
    // as small as possible for I²C transmission. This results in some
    // funny float math
    float ADCKP = analogRead(PIN_TRIM_KP) * 0.01; // Range 0 - 10.24
    float ADCKI = analogRead(PIN_TRIM_KI) * 0.01; // Range 0 - 10.24

    // Multiply by the scaling value from Kx_TRIM_SCALING
    // Use reinterpret_cast to ensure our int8 is correctly extracted from uint8 registerMap[]
    ADCKP *= static_cast<int8_t>(registerMap[TRIMMER_SCALE]) * 0.1; // Range -12.8 to 12.7
    ADCKI *= static_cast<int8_t>(registerMap[TRIMMER_SCALE]) * 0.1; // Range -12.8 to 12.7

    // ADCKx could very well be too large for int16 Kx_VALUE but because we used the correct
    // precision in all of the math up until now, we can simply truncate the result and all
    // we lose are a few decimals of precision that we don't want to store anyway
    registerMap[KP_VALUE] = int16_t(ADCKP * 100) >> 8;
    registerMap[KP_VALUE + 0x01] = int16_t(ADCKP * 100);
    registerMap[KI_VALUE] = int16_t(ADCKI * 100) >> 8;
    registerMap[KI_VALUE + 0x01] = int16_t(ADCKI * 100);
}

/****************************************************
 * Function updateSettings()
 * Check that our devicce settings still match those 
 * found in the register map. If not, change the device
 * settings then reset the change flag. 
 * This gets called every loop directly after a device 
 * register is written to. 
****************************************************/
void updateSettings()
{

    // Check if the device address has been changed
    // Compare against global var wire_addr which is
    // unchanged since last Wire.begin() call
    if ((registerMap[WIRE_ADDR] != wire_addr) && registerMap[WIRE_ADDR] > 0x07 && registerMap[WIRE_ADDR] < 0x78)
    {
        wire_addr = registerMap[WIRE_ADDR];
        // store the I²C Address in EEPROM so it sticks around on reboot
        EEPROM.put(EEPROM_DEV_ADDR, wire_addr);
        // restart I²C
        Wire.end();
        Wire.begin(wire_addr);
        Wire.onRequest(requestEvent);
        Wire.onReceive(receiveEvent);
    }else{
      registerMap[WIRE_ADDR] = wire_addr;
    }

    // The following are easy to evaluate and don't
    // touch EEPROM so we go ahead and "update" them
    // every time whether they've been changed or not

    // FAN ENABLE
    if (registerMap[FAN_ENABLE] == 0xFF)
    {
        digitalWrite(PIN_FAN_ENABLE, HIGH);
    }
    else
    {
        digitalWrite(PIN_FAN_ENABLE, LOW);
    }

    // Reset the flag
    changeFlag = 0;
}

/****************************************************
 * Function setWireAddress()
 * Check if there is a device address stored in EEPROM
 * If there is, set it. If not, store the factory default
 * and set that.
****************************************************/
void setWireAddress()
{
    uint8_t eepromVal;
    EEPROM.get(EEPROM_DEV_ADDR, eepromVal);
    if (eepromVal == 0xFF)
    {
        EEPROM.put(EEPROM_DEV_ADDR, DEFAULT_ADDR);
        registerMap[WIRE_ADDR] = DEFAULT_ADDR;
    }
    else
    {
        wire_addr = eepromVal;
        registerMap[WIRE_ADDR] = eepromVal;
    }
}

/****************************************************
 * Function readTachometer()
 * Read the pulse length of the Fan Tachometer and 
 * convert to real RPM. Cast to 2 bytes and store in 
 * appropriate register location
****************************************************/
void readTachometer()
{
    long tach; // Pulse length of tachometer pulse in microseconds
    long freq; // Frequency of tachometer pulse in Hz derived by (1000000 / pulse length in microseconds) / 2 transitions per pulse
    long rpm;  // RPM derived by (frequency / pulses per revolution) x 60

    tach = pulseIn(PIN_TACH_IN, LOW); // Get pulse length of tachometer pulse, from this we can derive the fan speed
    if(tach>0 && registerMap[FAN_TACH_DIVIDER] > 0){
      freq = 1000000 / tach / 2;
      rpm = (freq / registerMap[FAN_TACH_DIVIDER]) * 60;
    }else{
      rpm = 0;
    }

    registerMap[FAN_ACTUAL_RPM] = uint16_t(rpm) >> 8;
    registerMap[FAN_ACTUAL_RPM + 0x01] = uint16_t(rpm);
}

/****************************************************
 * Function fastPWMSetup()
 * Setup the appropriate timer registers on the Attiny841
 * to output FastPWM on OC1B, compare to ICR1 for TOP.
 * In FastPWM mode, TCNT1 will count up to TOP and then
 * reset. Output Compare is cleared when they match. 
****************************************************/
void fastPWMSetup()
{
    TCCR1B = 0; // Clear Timer Control Register 1B
    TCNT1 = 0;  // Clear Timer1

    TCCR1A &= ~_BV(WGM10); //FastPWM mode with ICR1
    TCCR1A |= _BV(WGM11);
    TCCR1A |= _BV(WGM12);
    TCCR1B |= _BV(WGM13);

    TCCR1A |= _BV(COM1B1); // Compare Output Mode Channel B (Non-Inverting Mode)
    TCCR1A &= ~_BV(COM1B0);

    TCCR1B |= _BV(CS10); // No Prescaler
    TCCR1B &= ~_BV(CS11);
    TCCR1B &= ~_BV(CS12);

    ICR1 = 320; //FastPWM mode counts up 320 (25kHz)
    OCR1B = 0;  //0-320 = 0-100% Width cycle
}

void pwmWidth(int width)
{
    // Change the width of the PWM wave generator
    // Maximum width is 320 cycles (100% duty)
    OCR1B = constrain(width, 0, 320);
    // Store the speed that we're setting the fan
    // as a proportion of the maximum (essentially
    // the inverse of the PWM duty cycle)
    registerMap[PROPORTIONAL_THROTTLE] = uint8_t(map(width, 0, 320, 0, 100));
}

/****************************************************
 * Function requestEvent()
 * Handle requests from the I²C controller
 * Emulate a proper I²C peripheral by writing out the 
 * contents of the last received register index and 
 * then increment the index for consecutive reads.
 * Register index is reset whenever new bytes are 
 * received so it can't run away.
****************************************************/
void requestEvent()
{
  for(uint8_t idx = registerIndex; idx < sizeof(registerMap); idx++)
  {
    Wire.write(registerMap[idx]);
  }
}

/****************************************************
 * Function receiveEvent(int bytesReceived)
 * Handle incoming bytes from I²C controller
****************************************************/
void receiveEvent(int bytesReceived)
{

    /* If we receive a single uint8_t, we can assume the controller is asking for the contents of a register 
   so we store the uint8_t in a global var that we can retreive during requestEvent() */

    for (int a = 0; a < bytesReceived; a++)
    {
        if (a < MAX_SENT_BYTES)
        {
            receivedCommands[a] = Wire.read(); //grab stuff and jam it into the command buffer
        }
        else
        {
            Wire.read(); //if we receive more data than allowed, chuck it
        }
    }

    if (bytesReceived == 1 && (receivedCommands[0] < sizeof(registerMap))) //if we got a uint8_t within the register map range, keep it
    {
        registerIndex = receivedCommands[0];
        return;
    }

    if (bytesReceived == 1 && (receivedCommands[0] >= sizeof(registerMap))) //if we got a uint8_t outside the register map range, chuck it
    {
        receivedCommands[0] = 0x00;
        registerIndex = 0x00;
        return;
    }

    /* If we receive multiple bytes, the first is a register address and the following 
    are values to write starting at the specified address */

    if (bytesReceived > 1)
    {
        // load received bytes into consecutive register addresses
        for (int i = 0; i < bytesReceived - 1; i++)
        {
            registerMap[(receivedCommands[0] + i)%sizeof(registerMap)] = receivedCommands[1 + i];
            
        }
        changeFlag = 1; // Set the change flag
    }

    return;
}

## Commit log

2021-07-19 x01 PCBs ordered
    [qwiic_blower-Panel.GBL, qwiic_blower-Panel.GBO, qwiic_blower-Panel.GBP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]
2021-12-06 V1 Docs and Housecleaning
    [qwiic_blower-Panel.GBL, qwiic_blower-Panel.GBO, qwiic_blower-Panel.GBP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]
2022-01-09 Firmware v11
    Firmware update to address bugs filed by dlkeng
    - Enforce basic I2C Address validity
    - readTachometer() now returns 0 if asked to divide by 0 (instead of attempting it and crashing)
    - requestEvent() now writes all registers to the buffer starting at the requested index and ending at sizeof(registerMap) so it cannot run away
    - receiveEvent() now wraps incoming bytes when reaching the end of the register map
    - Add firmware version register (reports version 11)
    [Qwiic_Fan_Controller.ino]
2022-01-12 Add "Programming" directory
    - batch_program.bat will correctly program the fuse bits and flash using an attached AVR Pocket Programmer
2022-01-12 Update batch_program.bat
    - changed fuse bits to set the brownout detection to 2.7v

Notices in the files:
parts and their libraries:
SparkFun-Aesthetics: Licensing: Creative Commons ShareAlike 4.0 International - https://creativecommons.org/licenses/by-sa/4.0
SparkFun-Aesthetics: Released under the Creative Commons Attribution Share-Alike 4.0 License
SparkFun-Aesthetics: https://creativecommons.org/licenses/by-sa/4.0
